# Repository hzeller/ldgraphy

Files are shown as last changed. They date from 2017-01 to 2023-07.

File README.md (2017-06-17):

LDgraphy - Laser Direct Lithography
===================================

http://ldgraphy.org/

A process also known as Laser Direct Imaging.

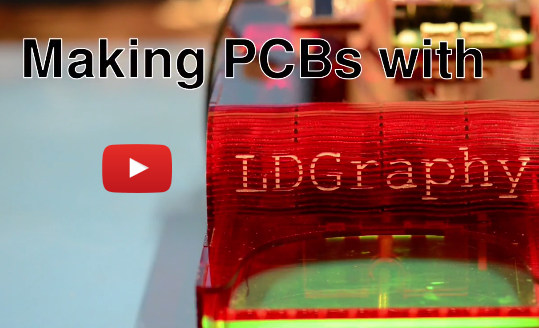
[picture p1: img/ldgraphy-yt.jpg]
First Test
[](https://youtu.be/G9-JK2Nc7w0)

Simple implementation of photo resist exposure using a 405nm laser.
Goal is to have this Open Source/Open Hardware system easy to reproduce with
commonly available parts. The BOM is in the order of $100 including the
Beaglebone Green.

  * 500mW 405nm laser ($30ish)
  * Commonly available polygon mirror scanner (from laser printers) ($20ish)
  * Beaglebone Black/Green to control it all (using the PRU to generate precise
    timings for motors and laser) ($40ish)
  * Stepper motor for linear axis (plus end-stop switches) (scrap box)
  * Photo diode to determine start-of-line (as the polygon mirrors have
    slightly different long faces and also phase-drift over time) (SFH203P)
  * Local electronics: fast Laser diode driver and stepmotor driver (few $$)

Stay tuned for a putting-it-together video once the design is settled.

Here is some [rough design outline][design] in case you are interested in more
details.

Work in Progress
----------------
Currently, the design is [work in progress][LDGraphy-posts] while testing
various different types of commonly available polygon mirrors and lasers. The
[PCBs](./pcb) for the [cape] and the [laser current driver] are in their
first iteration with more focus on easy measurements and removable parts
(e.g. stepper driver and DC/DC converter are external modules) than compact
design. This part of the hardware is likely to change in the
short term; it turns out, for instance, that some polygon mirrors have not
perfectly perpendicular faces. So an additional sensor is needed to correct
for that.

And of course, the software would need a little more bells and whistles
(e.g. a web-server to easily upload Gerber designs).

Having said that, the device is fully operational with a reliable
resolution of ~0.15mm/6mil, which is right up there with basic fab-house
offerings (goal: reliable 0.1mm (4mil) traces and clearance).

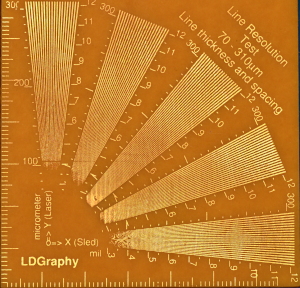
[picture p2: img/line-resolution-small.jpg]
Resolution test
[][resolution]

Compile
-------
This compiles on a BeagleBone Green/Black; it requires the PRU on these
computers for hard realtime-switching of the Laser.

```
git clone --recursive https://github.com/hzeller/ldgraphy.git
```

Install relevant packages. We are reading png-images as input, so we need the
library that helps us with that (probably already installed on your system):
```
sudo apt-get update
sudo apt-get install libpng-dev -y
```

Then compile:
```
cd ldgraphy/src
make
```

To properly prepare the GPIOs and the PRU to be used, you have to install
the device tree overlay on your Beaglebone:
```
cd ldgraphy/device-tree
sudo ./start-devicetree-overlay.sh LDGraphy.dts
```

The input is a PNG image. For converting Gerber files to PNG, see the
`gerber2png` tool in the [scripts/](./scripts) directory.

Usage:
```
Usage:
./ldgraphy [options] <png-image-file>
Options:
        -d <val>   : Override DPI of input image. Default -1
        -i         : Inverse image: black becomes laser on
        -x<val>    : Exposure factor. Default 1.
        -o<val>    : Offset in sled direction in mm
        -R         : Quarter image turn left; can be given multiple times.
        -h         : This help
Mostly for testing or calibration:
        -S         : Skip sled loading; assume board already loaded.
        -E         : Skip eject at end.
        -F         : Run a focus round until Ctrl-C
        -M         : Testing: Inhibit sled move.
        -n         : Dryrun. Do not do any scanning; laser off.
        -j<exp>    : Mirror jitter test with given exposure repeat
        -D<line-width:start,step> : Laser Dot Diameter test chart. Creates a test-strip 10cm x 2cm with 10 samples.
```

Case
----
The current version is made out of [laser-cut acrylic](./hardware)
parts to have it easily and cheaply build for everyone who has
access to a laser cutter (hint: your local Hackerspace might have one).

Here, all electronics is mounted on the top for easier measurements and
such. The final version will fit everything inside.

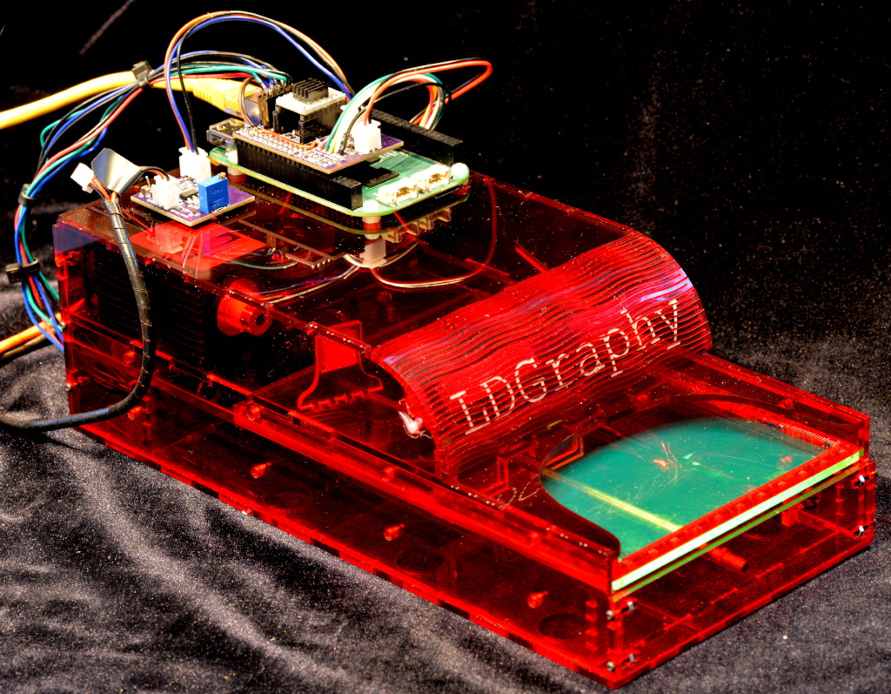
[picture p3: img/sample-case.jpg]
Case
[](./hardware)

Above is current status of the case, which went through some refinements (here
an [earlier case](./img/intermediate-case.jpg) which better shows
the internal arrangement).

This was the first experiment
-------------------------------

#### First Light

| Setup | Result
|---|---
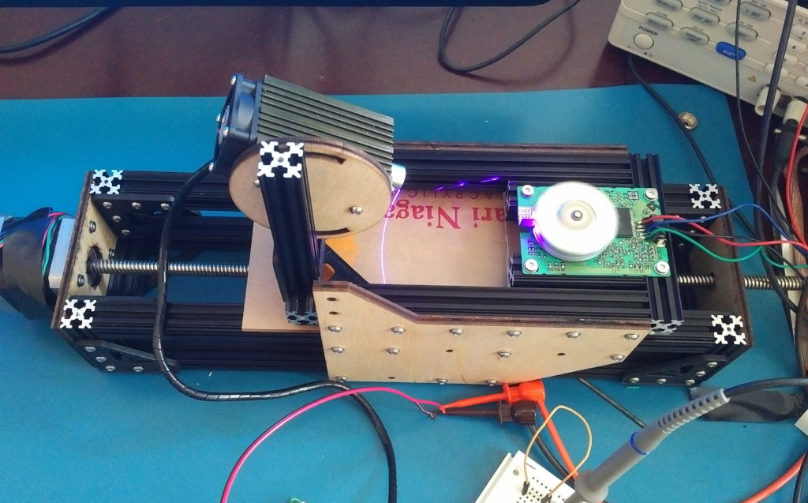
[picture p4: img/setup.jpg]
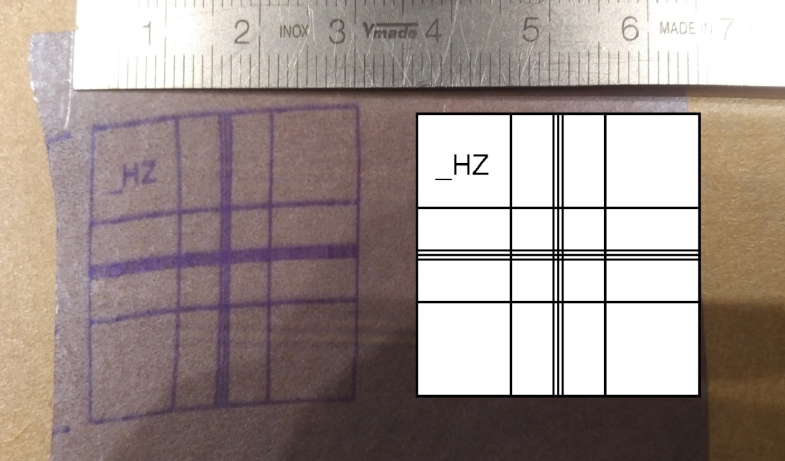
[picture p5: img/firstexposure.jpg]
|  | 

The first test-device was put together with extruded aluminum.
Somewhat crappy first result, but had potential. Exposure time for this 30 mm
long patch was around 90 seconds (for reference: on the right is how the
geometry _should_ look like).

As you can see, the early stages had some issues, e.g. you can't trust the "PLL"
of the mirror to properly lock - it has a phase drift over
time (hence the warped square). The current design has a HSync line sensor.
Overall the [progress] after that improved various
issues seen up to the point where it starts to be usable for PCB work.

[progress]: https://plus.google.com/u/0/+HennerZeller/posts/FeqdPoEZ3AT
[Laser current driver]: ./pcb/laser-drive
[Cape]: ./pcb/cape
[LDGraphy-posts]: https://plus.google.com/u/0/s/%23ldgraphy/top
[run-vid]: ./img/ldgraphy-yt.jpg
[resolution-thumb]: ./img/line-resolution-small.jpg
[resolution]: https://plus.google.com/u/0/+HennerZeller/posts/a8taHWeL5CC
[design]: ./design.md
[case-pic]: ./img/sample-case.jpg

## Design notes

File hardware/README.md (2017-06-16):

Casing
------

The [laser-cut-case.ps](./laser-cut-case.ps) PostScript file is a somewhat
parametrized source for making an acrylic case for LDGraphy.

Use black or dark-red acrylic for all parts except the sled to prevent the
405nm laser to escape in eye-damaging levels. The sled should be cut from
fluorescing material.

**Do not** use glass-clear transparent acrylic for the real machine, a 500mW
laser can blind you!

### How to cut
The file covers several parts, and depending on which you can fit
on your acrylic sheet and/or which you have to re-do, you can choose the ones
to be output in the first section that defines the
[`/print-...`](./laser-cut-case.ps#L28) boolean variables.

The Makefile can create a dxf file that is then usable in any laser cutter, just
call `make`.

There are several colored output layers that have different meaning for your
set-up in the laser cutter:
  * the 'green layer'. Set to scan engraving.
  * the 'blue layer'. Set to vector engraving.

Do the engravings first. Then:
  * the 'black layer'. Cut with outward kerf correction (laser cuts outside).
  * the 'red layer'. Cut with inside kerf correction (laser cuts inside).
  * the 'yellow layer': Set to straight cut, no kerf correction.

Don't cut
  * the 'gray layer' (if `/print-measures` true). Don't cut. Just FYI with measurements and help-lines.

### Customization
If you have a different size PCB that you want to expose, you can customize
the values in the PostScript file an generate a new DXF that should fit your
use-case. Be aware that wider boards means wider exposure angle which in
turn means more variation in focus distance (i.e. on average less sharp image).

Start with modifying `/pcb-w-mm` and `/pcb-h-mm`, watch the PostScript file in
a viewer (e.g. okular). It helps to switch on `/print-measures` while doing
these modifications for more information.
Now, modify the `/scan-angle` so that the polygon mirror fits on the top panel.
You might also need to change `/scan-redirect-mirror-distance` to have the
redirect mirror or its reflected beam not conflict with any object.

### Note
Nearing final state, ready to be used. This is fully parametrized, but
PostScript is not the very best 2D CAD software and updating things is not
so easy. I'd be happy if someone could translate that
into e.g. [Solvespace] CAD. Pull requests welcome :)

### Cut pattern

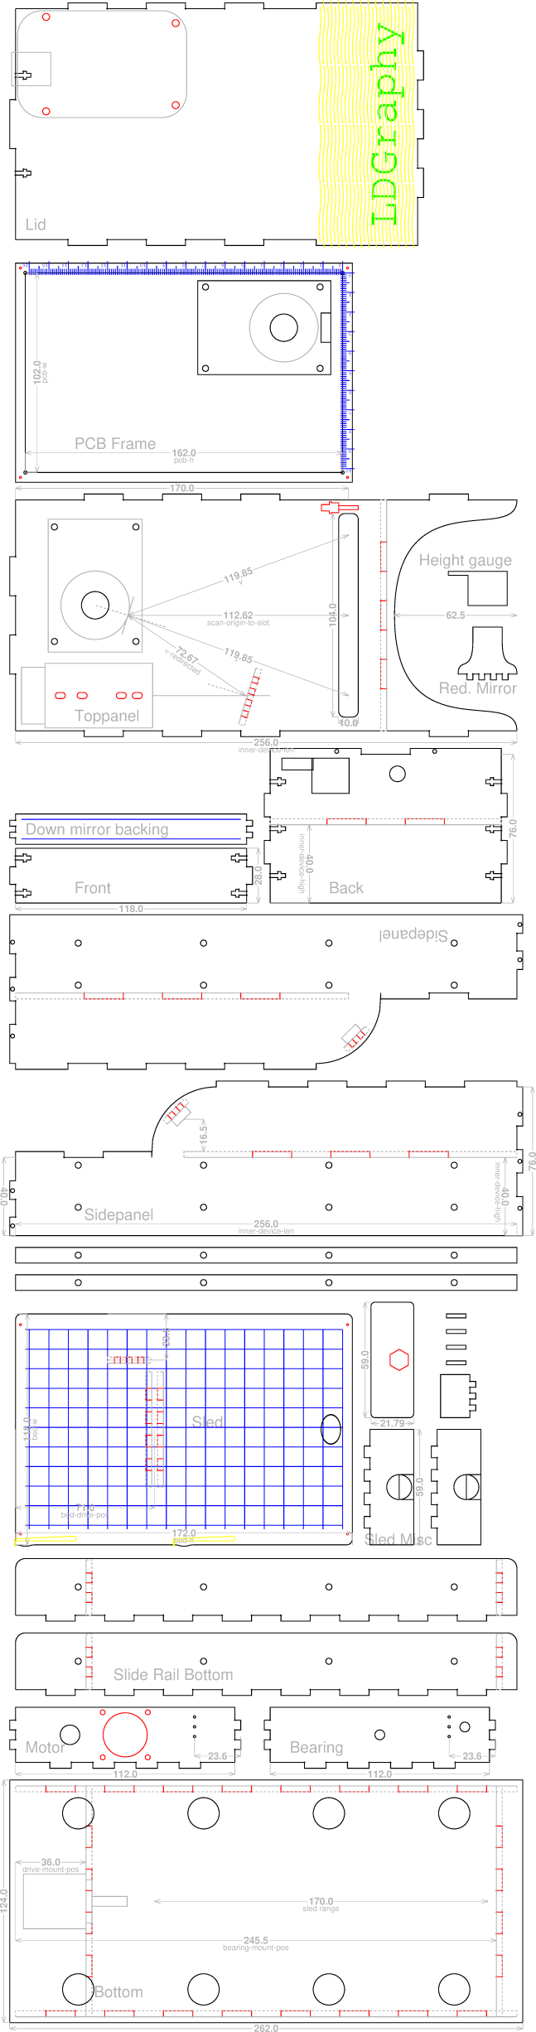
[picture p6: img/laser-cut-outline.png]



[Solvespace]: http://solvespace.com/

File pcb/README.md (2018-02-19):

LDGraphy PCBs
=============

Some boot-strapping required ... we need these PCBs first, before we can make
PCBs :)

  * [Laser driver](./laser-drive): fast current source to drive Lasers. Often,
    the Lasers you can buy come with their own driver, but they are very slow.
    This one is meant to switch >= 1Mhz while behaving as a current source.
  * [Beaglebone cape](./cape): a cape for the
    Beaglebone Black or Green providing all the connections to various
    parts of the set-up. This was the first version mostly for experimenting
    and successfully used.
  * [PocketCape](./pocket-cape): The new cape, ready for the cheaper
    and smaller PocketBeagle.
    Unlike the experimental board that used a DC/DC converter and stepmotor
    driver as separate modules, this has everything on-board.
    It is ready for double-sided boards with two outputs for lasers, polygon
    mirrors and two inputs for horizontal sync detection.

In the current set-up, they are mounted externally to provide easy access for
measuring various aspects. After the dust settles, they will all fit in the
LDGraphy case.

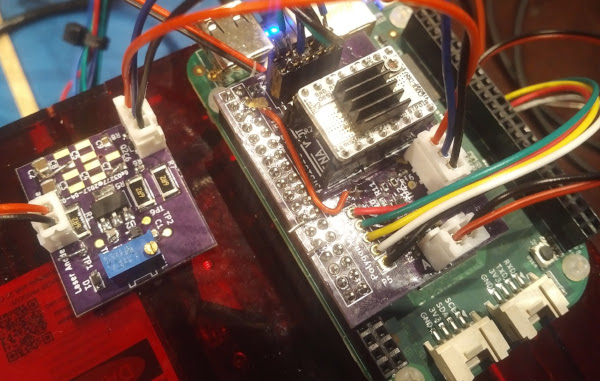
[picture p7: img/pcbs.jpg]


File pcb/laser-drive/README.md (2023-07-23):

Laser Driver Board
===================

Laser driver board, a fast current source switchable with a TTL input. Place
this as close as possible to the Laser with short wires.

Choose `R1`, `R5` and `R7` to achieve desired target current for given laser
(`I ≈ (Vref - 0.6) / (R5+R7)`; Vref=0V..5.6V).

Adjust desired current by reference voltage with trimmer before connecting
laser. Measure current through laser via `(+12V - TP4) / R1`.

Depending on the inductivity of the supply line or desired current, not all
of the 10μ caps (C2..C8) might be needed.

### BOM

Qty | Reference(s)              |  Value    |   Footprint
----|---------------------------|-----------|-----------------------------
2   | C1, C11                   | 100n      | 0603
7   | C2, C3, C4, C5, C6, C7, C8| 10u       | 1210
1   | C9                        | 100n      | 0805
1   | C10                       | 100p      | 0603
1   | D1                        | 5V6 zener | SOD-323
1   | J1                        | CONN_01X03| JST_EH_B3B-EH-A_1x03_P2.50mm
1   | P1                        | LaserOut  | JST_EH_B2B-EH-A_1x02_P2.50mm
1   | Q1                        | BCP5616Q  | SOT-223-3
1   | Q2                        | DMN2058UW | SOT-323_SC-70
3   | R1, R5, R7                | 6R2       | 2512
1   | R2                        | 2k2       | 0603
1   | R3                        | 470       | 0603
1   | R6                        | 680       | 0603
1   | R8                        | 1k        | 0603
1   | RV1                       | 10k       | Multi-turn trimmer (through-hole, 2.54mm pitch)
1   | U2                        |  MIC920   | SOT-353_SC-70-5

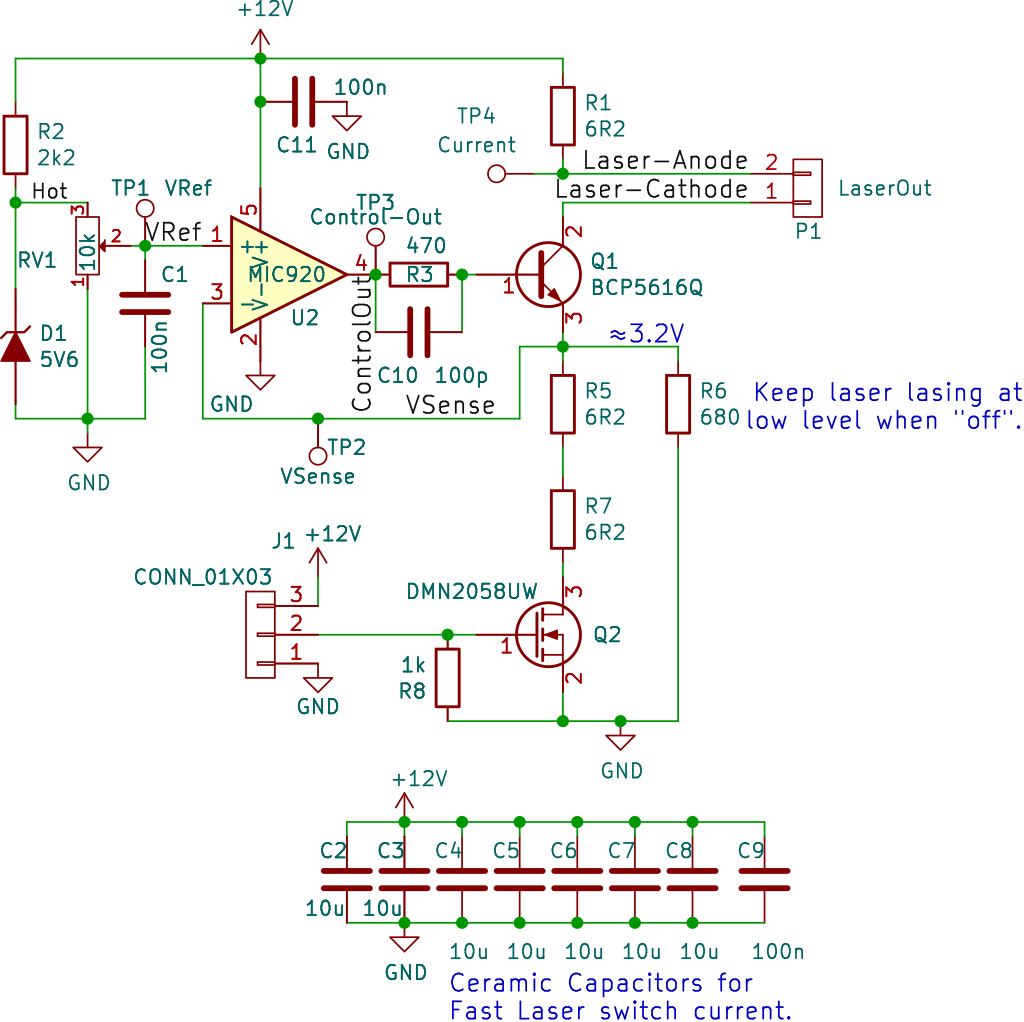
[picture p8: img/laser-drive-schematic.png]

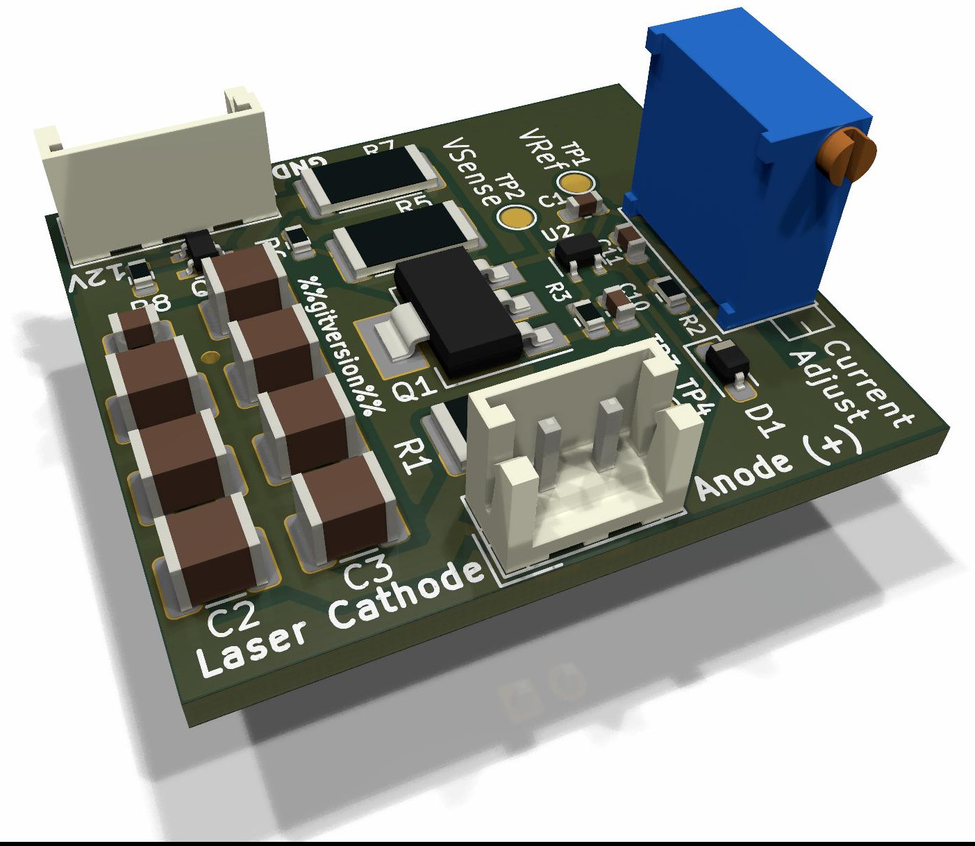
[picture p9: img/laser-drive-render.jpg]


There are probably better ways to have a fast current switching driver for
lasers that don't have a feedback line. Suggestions welcome.

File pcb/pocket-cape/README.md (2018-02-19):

PocketBeagle LDGraphy cape
==========================

A cape for the PocketBeagle, that will allow to expose double-sided boards.

*Work in progress; won't yet work with the current software and case.*

Not only the software is not adapted yet, but this assume as motor
the 28BYJ-48, yet the acrylic case is still using the larger stepper.

So if you want to build something now, I suggest to use
the [experimental cape](../cape).

The board is packed with connectors; all of which are choosen in a way
that it very hard to connect to the wrong one:

| Designator | Type | Description
|---:|:---|:---
| J2 | 2p JST-XH | Supply voltage. 12-16V
| J5, J8 | 3p JST-PH | Laser1, Laser2 output
| J1, J3 | 2p JST-PH | Laser1, Laser2 sync input
| J6, J7 | 5p 0.1" header| Polygon1, Polygon2 mirror
| J4 | 5p JST-XH | Sled stepper 28BYJ-48
| J10 | 8p FFC 0.5mm  | Connector for 320x200 SPI display
| J9 | 4p JST-PH | User-interface buttons
| J11 | USB | USB connector for Wifi dongle

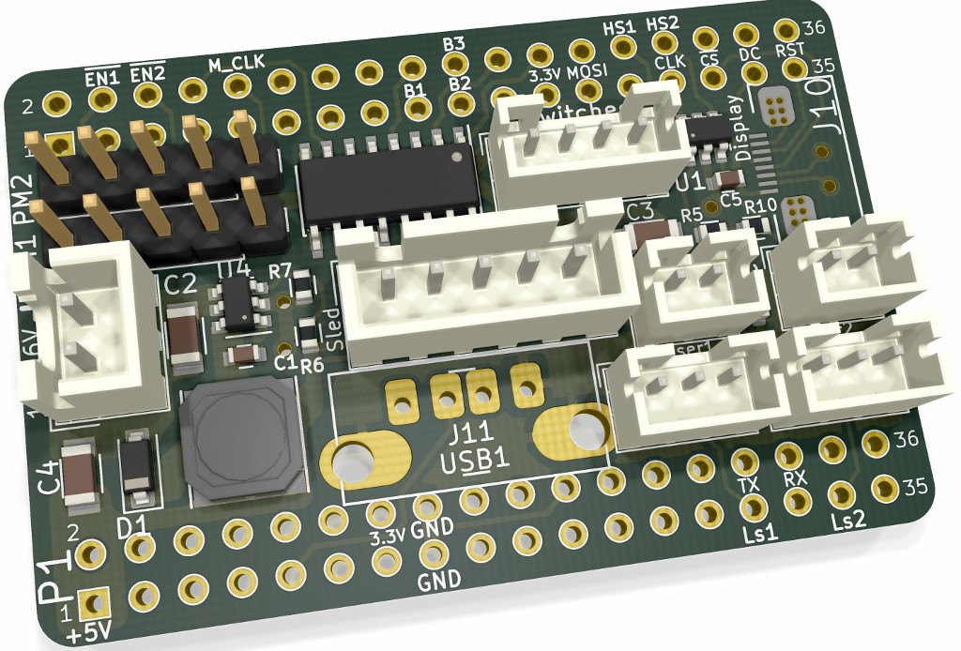
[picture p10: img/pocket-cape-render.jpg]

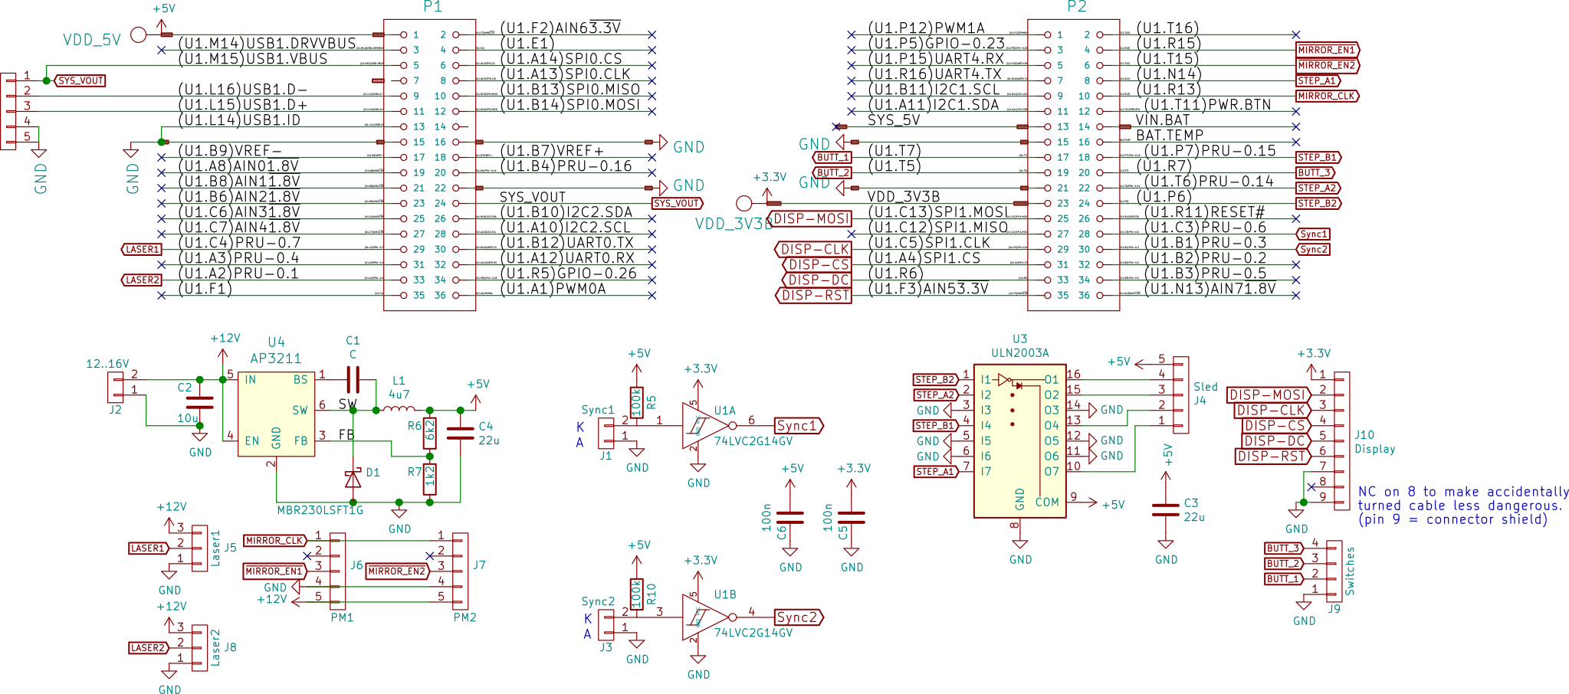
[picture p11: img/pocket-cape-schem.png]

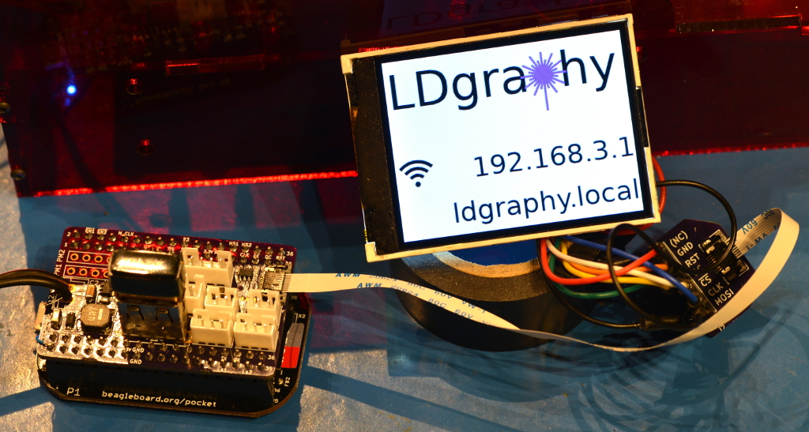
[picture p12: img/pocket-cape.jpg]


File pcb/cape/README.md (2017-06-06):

LDGraphy Beaglebone Black cape
==============================

This is for the experimental set-up. This is not meant to
be final, it focuses on easy measurement and mostly being a break-out for
connectors for other parts. The final board will have all the parts that are now
external modules integrated on one board.

  * Single 12V supply (uses a MP1584 based module to generate 5V supply for
    Beaglebone).
  * Inputs
     - Connector for photo diode used for the horizontal sync detection.
       Amplifier and Schmitt Trigger with fast OpAmps ([MIC920] datasheet)
       and steep enough slew-rate to generate acceptable output for digital
       inputs (also, same as used in the [laser driver](../laser-drive) to keep
       BOM small).
     - Two end-switches inputs.
     - One "user interface"-button input.
  * Outputs
     - Laser output connector for external [laser driver](../laser-drive).
     - Polygon mirror pulses and enable via 5-pin Polygon mirror connector.
     - Stepper motor (In this set-up: simply using a Pololu module)

(TODO: update schematic: there is now a cap accross R14)

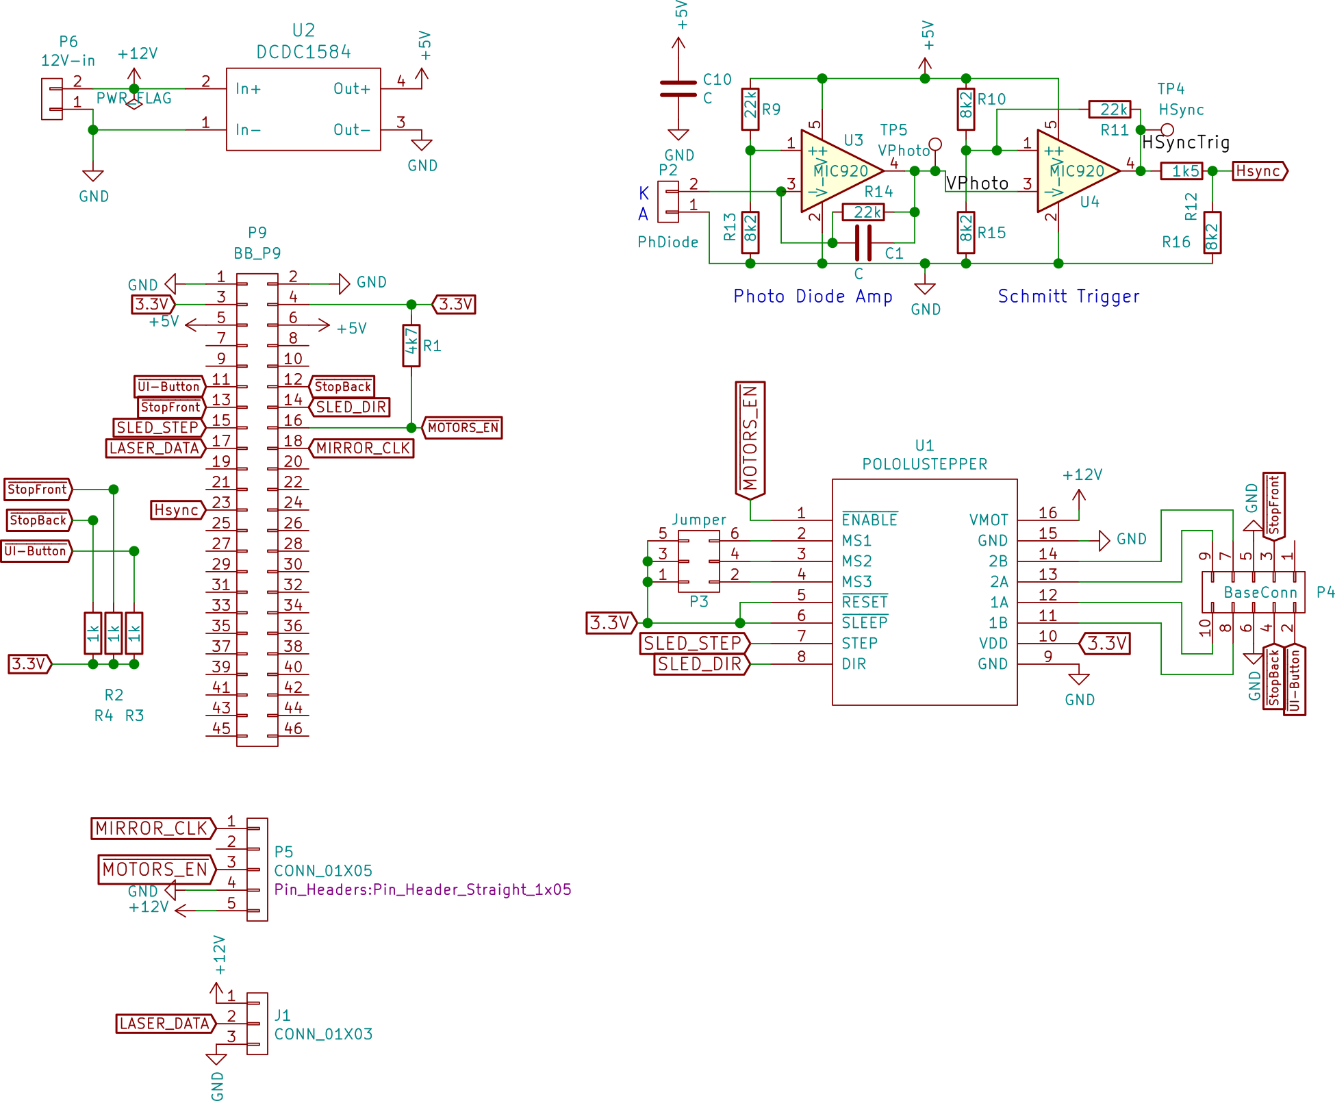
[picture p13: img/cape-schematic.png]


[MIC920]: http://ww1.microchip.com/downloads/en/DeviceDoc/mic920.pdf

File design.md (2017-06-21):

LDGraphy design overview
========================

### Theory

At its core, LDGraphy is a switched laser, a rotating mirror that
moves the dot in a scan-line and a sled that moves the photoresist-coated PCB
forward.

Laser scanning is very simple and cheap to do with common components these
days. Lasers with a wavelength of 405nm (which is close to the peak-sensitivy
of dry-film photoresist) can be found cheaply with around 500mW power.

As for scanning, there are several techniques. A common one is to have a mirror
that rotates to deflect a laser. Since it would take a while for a mirror
to turn around full 360° after a segment is scanned, they come as
a polygon mirror: a polygon that has mirror-reflective edges.
A typical mirror that is used in Laser printers 6 sides; you notice that
the actual mirror face is not that high - but we only need to deflect a laser dot.

| Top | Side
|---|---
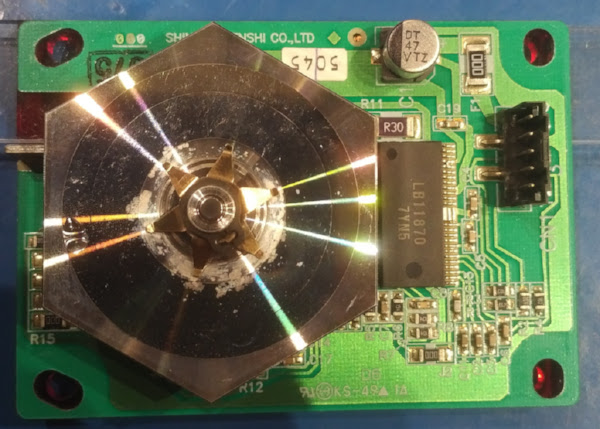
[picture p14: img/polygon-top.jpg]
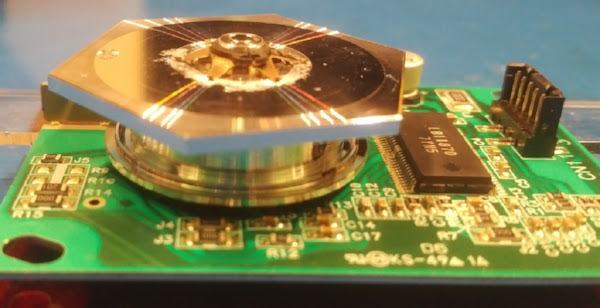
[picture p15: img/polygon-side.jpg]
|   | 

With this hexagon, we can project a 120° arc (each mirror
face is 60°, so the angle between incident ray and reflected ray is 120°).

Here, we just shine (a fast blinking) laser at an angle from the top, it is
reflected at the rotating mirror and projected downwards.
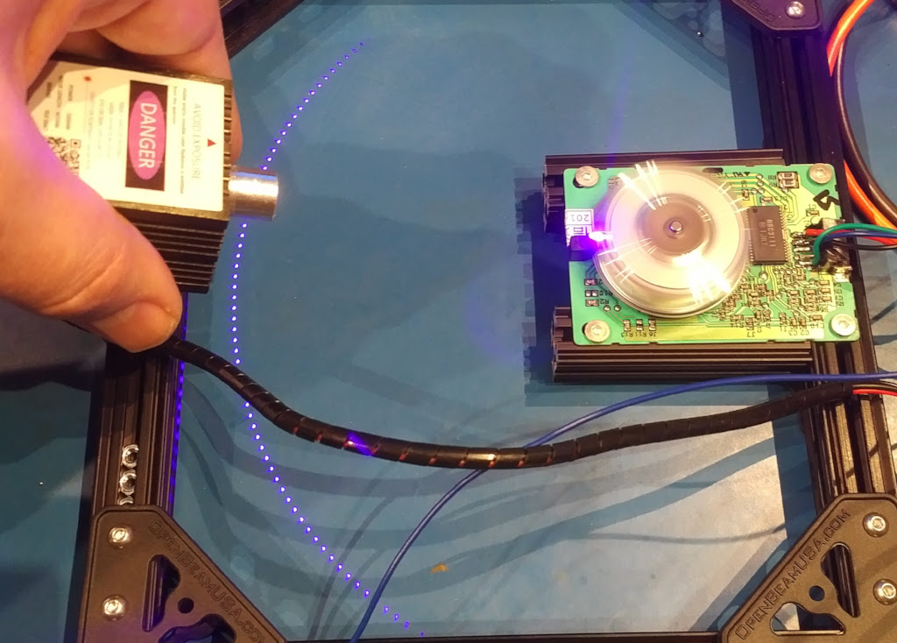
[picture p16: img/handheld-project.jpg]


#### Direct angled arc exposure
We can make a scanning device with this simple set-up if we correct for the
arc distortion in software; in fact, in an early experiment for LDGraphy
I was doing exactly that:

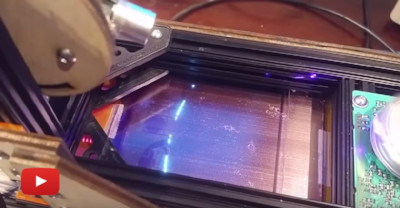
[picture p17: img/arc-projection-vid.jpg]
Early experiment
[][arc-project-vid]

There are advantages for this set-up: we can utilize a large fraction of the
laser on-time by covering the majority of the available scan range.
The scanning laser is "almost" in focus for the scan range where it hits
the board.

This is a simulation of such a scanning in which we use 105° out of 120°
(the laser is off only for 15 degrees). We can see that the laser dot is oval
in the extreme angles but also even in the center. This is because the actual
focal plane of the laser (indicated with a gray disc at the sharpest focus)
is hitting the surface at an angle, resulting in an oval exposure.

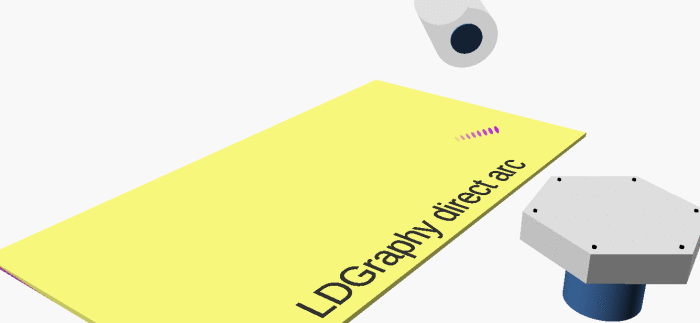
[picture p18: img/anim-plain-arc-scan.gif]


This set-up is very simple to build, but the oval exposure dot is an issue.
Also it is very sensitive to angle variations: just small changes in the
shallow angle moves the projected arc-line forward and backwards.

#### Cone mirror arc exposure
This could be fixed, if we had a mirror that points the laser-arc downwards, so
that it hits the resist perpendicularly and is also always in focus.
The mirror would need to be a circular segment with a downwards
angle -- essentially a segment of
an inner slice of a cone. Now we hit the photo resist always at a sharp
focus point, even for the wide scan angle of 105 degrees as the geometry
keeps the focal plane of the laser exactly on the exposed surface.

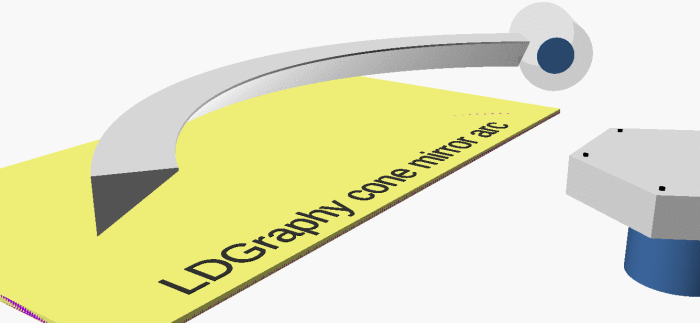
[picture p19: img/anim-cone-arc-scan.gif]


However, making custom mirrors in such a shape at home is not easy.

Possible ways:
 * With a lathe: this would essentially be a 45° bevel on the inside of a
   large diameter stainless steel pipe with a wall thickness of about 2-3mm.
   Then mirror finish polishing this bevel. Stainless steel or aluminum are
   both nicely polisheable, so these could be materials of choice.
 * [John M. suggests on his blog][NaN-cone-mirror] to build such a mirror using
   laser cut parts that, snapped together, defining the shape.

We want to build this machine with minimal accessible tools, so these techniques
have to be explored if they can be done with minimal tools. Till then, let's
see what else we can do.

#### Straight mirror line exposure
We can simplify and use a straight mirror to project downwards to get a line.
However, the focus point then is of course not always in the plane of the
photo sensitive material. In particular if we cover a large scan angle, the
focus variants are significant.

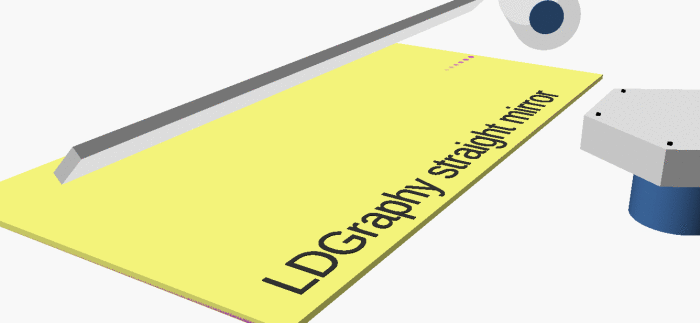
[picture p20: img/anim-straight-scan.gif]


The exposure point now is very large at the fringes. We could alleviate some of
it by "plunging" the focus plane below the surface at the center, but it will
still be too much of a variant.

The advantages for the home-build is, that this works with a very simple straight
mirror (easy to come by with) and does not have the problem of being sensitive
to the shallow angle variations like the angled direct arc exposure.

The issue though is the focus, even more pronounced than in the direct arc scan.

#### F-Theta lens corrected line exposure
In professional scanning applications, a so-called [f-theta lens][f-theta-images]
is used to keep a straightly projected laser dot always focused to a plane.

If you take apart a laser printer, you will see a lens set in the
laser assembly: that is the f-theta lens.

However, this is also somewhat out of reach for the hobbyist to make (though
I still consider to try making one with transparent acrylic). It also does not
seem to be available as off-the-shelf part like the Polygon mirrors and the laser
does (you can get them, but they are very expensive).

If you find some, it is probably meant for a laser printer and optimized for
infrared light not UV light.

What else can we do ?

#### Straight mirror line exposure with small throw

If we choose to do the straight projection, but only use the 'center piece'
and limit ourselves to a smaller angle, the focus variation is not _that_ much
and we get an acceptable compromise in exposure dot size.

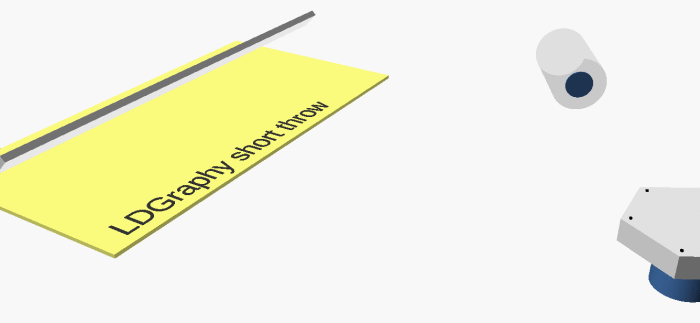
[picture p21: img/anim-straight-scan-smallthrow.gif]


We don't need any special mirror or lens. The disadvantage is, that we only
can use part of the time of the laser: if we use 40° scanning out
of 120°, we only use the laser for 1/3 of the time (you see the laser is
dark for a long period in the illustration). Also, we need much more space as
we need to be further away to cover the same PCB width.

### Design Options Review
Let's review our options

   * Angled direct arc exposure
     mirror:
       * :thumbsup: fewest parts needed; almost full use of the laser; No light losses.
       * :thumbsdown: focus plane intersects with exposed board at an angle creating oval dots; susceptible to small angle changes; large build.

   * Cone mirror arc exposure
       * :thumbsup: almost full use of laser; no light losses; hitting resist
       	  perpendicularly; always in focus; very compact.
       * :thumbsdown: Requires to build a custom shaped mirror.

   * Straight mirror line exposure with _large_ throw
       * :thumbsup: easy to build; very compact.
       * :thumbsdown: very noticeable focus issues in far angels.

   * F-Theta lens corrected line exposure
       * :thumbsup: Almost full use of the laser; hitting resist perpendicularly; always in focus.
       * :thumbsdown: Requires to build a custom shaped lens; might have optical
         losses in the material.

   * Straight mirror line exposure with _small_ throw
       * :thumbsup: easy to build; focus issues less pronounced than with
          large throw.
       * :thumbsdown: need longer exposure time; large build.

Overall, the most promising is the cone mirror solution: it creates sharp focus
points, makes good use of the laser time and building a custom mirror
is somewhat more feasible than building a f-theta lens.

However, since ease-of-build for everyone with limited access to tools is a
priority, we start with the small throw line exposure for this first version
of LDGraphy - it doesn't require any manufacturing of a mirror and is a
good compromise.

### Practice

#### Scanning

This is how the current LDGraphy device looks like. From the top, we can
see all relevant components for the laser scanning:

| Drawing | Reality
|---|---
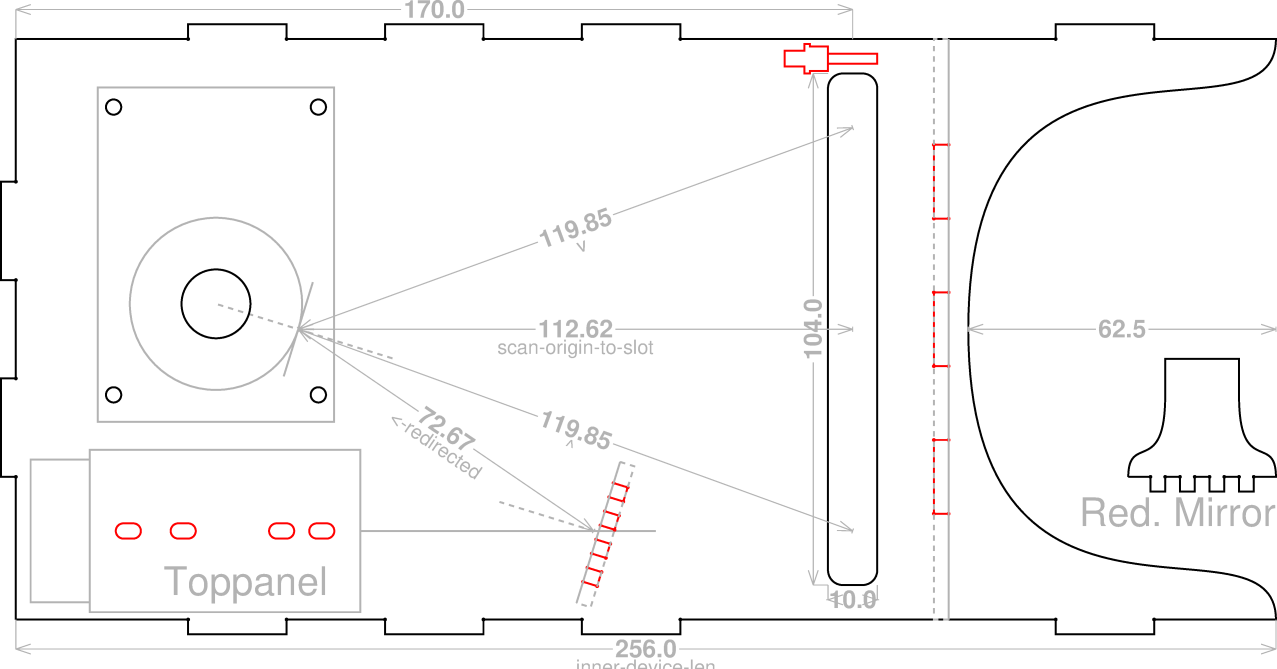
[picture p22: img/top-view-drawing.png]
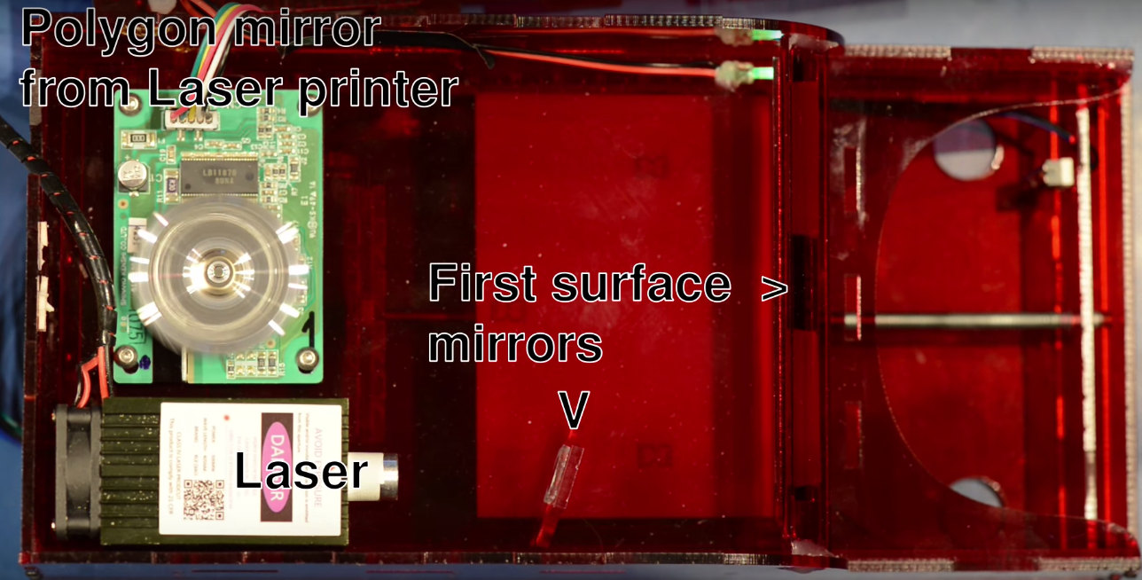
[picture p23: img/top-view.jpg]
|[See full drawing here][hardware] | 

To keep things more compact, the laser is mounted in one corner and the light
is redirected onto the polygon mirror. But other than that, this is exactly
as discussed above. There is a long mirror on the side that is pointing
downwards, a little hard to see from above, so lets look from the back, with
some rough indication of the laser path:

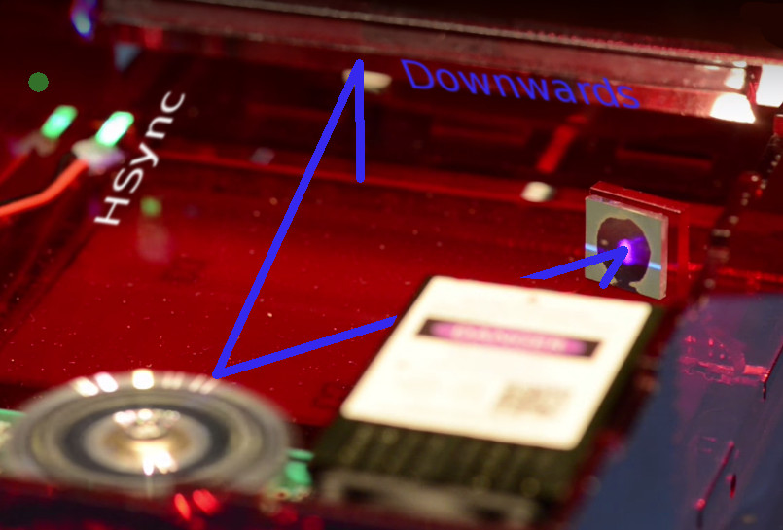
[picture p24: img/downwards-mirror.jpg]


When the polygon mirror is rotating, the laser point passes through a slit onto
the surface to be exposed.

On the left, you see a fluorescing piece of material that has a photo diode
attached. This is our horizontal sync (HSync) to detect when a laser line starts.

##### Issues

There is an issue that I discovered with some cheap polygon mirrors: the six
mirror faces have a little variation and not being entirely parallel to the
rotating axis, so project lines up and down a little, depending on the face.
So what needs to be done is to have another sensor to count mirror faces, and
then correct for this after a calibration step in software.

#### Moving the sled

The sled is moved with a stepper motor and a threaded rod. This rod does not
need to be CNC quality ball-screw, a simple screw from the hardware store is
sufficient. Why ? We only need to move in one direction, so we don't care about
backlash issues.

Here is how the base looks like, housing the motor and the threaded rod. The rod
is 'mounted' to the shaft of the motor with a heatshrink tubing (and a little
expoxy butting these together). A nut is not directly mounted to the sled but
to a slab of acrylic. You also see both the limit-switches:

| Just drive | .. with sled
|---|---
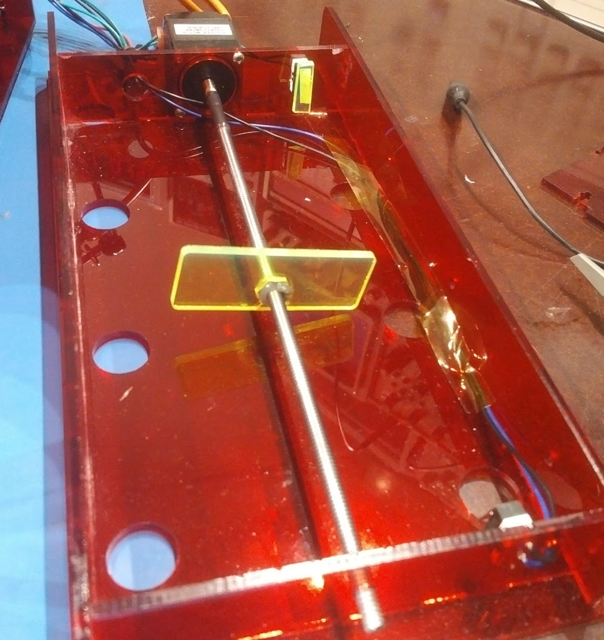
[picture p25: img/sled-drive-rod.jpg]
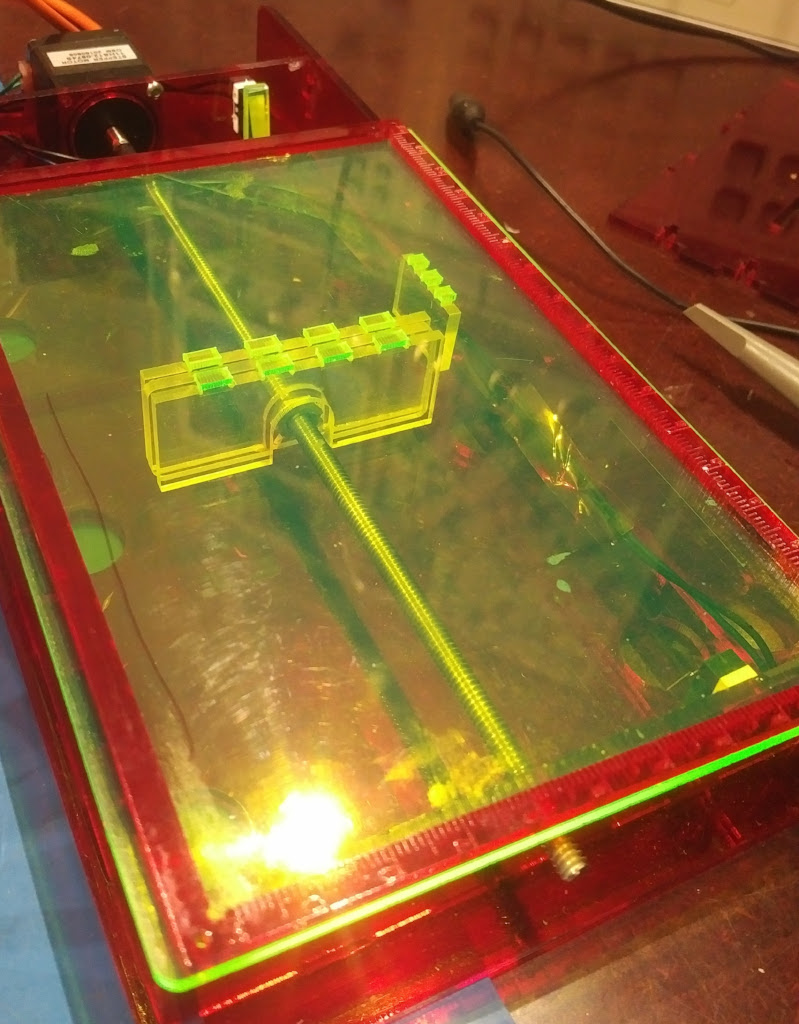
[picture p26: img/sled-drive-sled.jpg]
| | 

This allows us to have a separate sled that then sits on top of the moving
slab of acrylic. The design detail here is, that it allows to drive the sled
forward and backward, but has freedom to move in other directions: this can
be used to essentially be immune to 'wobble' from the cheap threaded rod.
In the current test version of LDGraphy, I have a horribly wobbling rod that
I found in a corner of my workshop.

You [see the wobble in the video :movie_camera:][ldgraphy-vid]; It still produces
acceptable quality

[Resolution test][resolution]

#### Electronics

Everything is controlled by a BeagleBone Black or Green. It has the nice property
that it is a common ARM machine running Linux (so offers the comfortable
environment of a full operating system including networking and can do all the
work like converting Gerbers and do image processing), but it also has
a built-in Programmable Realtime Unit (PRU) - a fast (200Mhz), independent
microcontroller essentially to help do the timing-accurate parts interfacing
the hardware.

We need this to accurately
generate the pulses to control the polygon mirror, switch on the Laser at the
right times (we have about 2Mhz pixel clock), and generally keep track of where
the laser is. And before you ask: of course, this could be done with an external
Cortex M4 or so, connected via SPI to some other computer (it would be more
expensive of course, but it works). I just had the BeagleBone lying around and
had used the PRU in a [previous project][beagleg].

The laser requires a current source, in our case it needs to be switched in the
low Mhz range. Some lasers (that you get from e.g. Aliexepress) already have a
"TTL driver", but they are utterly low frequency (50ish kHz), so this is why this
project needed its own [laser current driver] (not perfect yet, but works).

Right now, all the electronics is attached to the outside of the case, for easy
hacking and scope-probe access. Eventually, all these parts will
go inside the case.



[resolution-thumb]: ./img/line-resolution-small.jpg
[resolution]: https://plus.google.com/u/0/+HennerZeller/posts/a8taHWeL5CC
[beagleg]: https://github.com/hzeller/beagleg
[Laser current driver]: ./pcb/laser-drive
[early-experiment]: ./img/arc-projection-vid.jpg
[arc-project-vid]: https://youtu.be/8tyT4CI-1io
[ldgraphy-vid]: https://youtu.be/G9-JK2Nc7w0
[hardware]: ./hardware#cut-pattern
[f-theta-images]: https://www.google.com/images?q=f+theta+lens
[NaN-cone-mirror]: http://notanumber.net/archives/228/circular-mirror-idea-laser-lithography

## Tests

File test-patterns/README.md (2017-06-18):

Test Patterns
=============
Various test-patterns used to calibrate and test the machine.
Postscript files, use Makefile to generate hi-res PNG that can be fed to
LDGraphy.

#### Low res examples

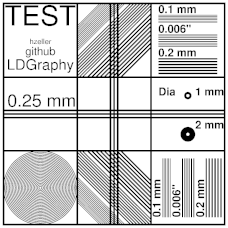
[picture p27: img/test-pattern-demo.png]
test-pattern

[test-pattern](./test-pattern.ps)

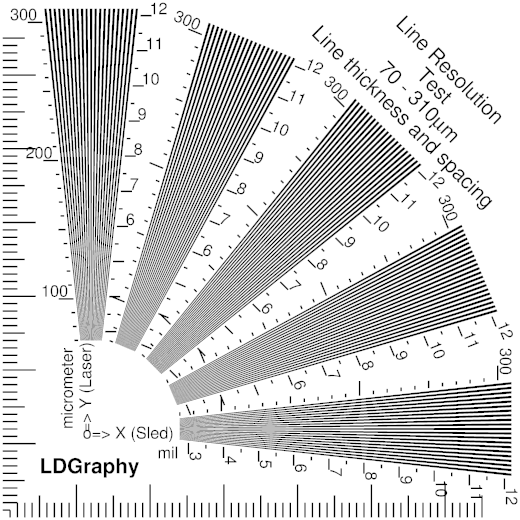
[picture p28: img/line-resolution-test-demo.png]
line-resolution-test

[line-resolution-test](./line-resolution-test.ps)

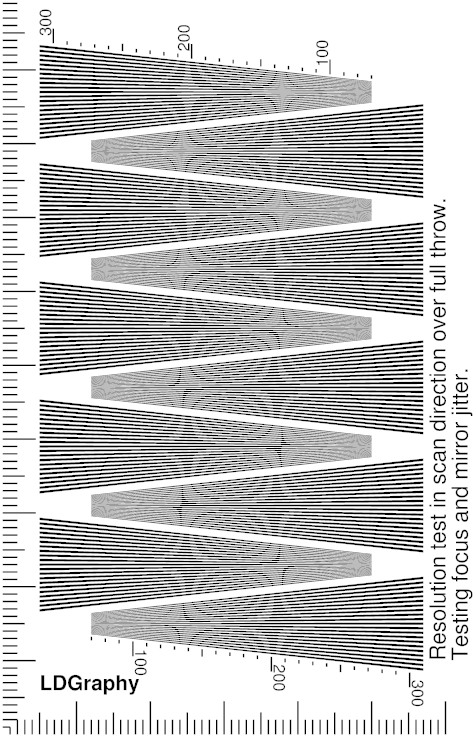
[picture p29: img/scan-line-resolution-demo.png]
scan-line-resolution-demo

[scan-line-resolution-demo](./scan-line-resolution.ps)

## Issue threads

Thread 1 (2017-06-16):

Raspberry Pi instead of beaglebone

jvegaf, 2017-06-16:
First of all congrats for the project, it's awesome !!!

Why you use beaglebone ?

It's possible use a raspberry pi ?

Thanks !

hzeller, 2017-06-16:
Only if you use and program an external fast microcontroller to sent the laser pulses at the right time. Right now, LDGraphy relies on the Programmable Realtime Unit of the BeagleBone to do that.
The BeagleBone Green is $39, the Raspberry Pi $35, so that is $4 well worth spent for reduced complexity.

Closed 2017-06-16.

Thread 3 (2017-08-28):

Not an issue, but a (stupid) question

Pepetruen0, 2017-08-28:
Hi, I'm seeing that the laser driver has a note stating "there is now a cap accross R3." As I'm a newbie and English is not my primary language, can I have a brief explanation of what this means? Also, what size capacitor do I need to use for this?

Thanks.

hzeller, 2017-08-29:
This means that there needs to be an additional capacitor in parallel to `R3`, which has not been reflected yet in the schematic or printed circuit board.
I have fudged the capacitor in with what I had lying around, I think it was around 100pF.

Pepetruen0, 2017-09-04:
Wait, when you say "fudged" do you mean "I got away with" or "totally destroyed"? Just to be sure.

hzeller, 2017-09-05:
'fudged' means that I choose the value without much calculation after having measured the outcome on an oscilloscope. I hacked it into the existing board by just soldering the capacitor on top of the R3. It works well.

Not sure what you want to do with your circuit above, but the 100pF needs to be across `R3` not `R2`.

Pepetruen0, 2017-09-05:
Whoops, my bad. I meant something like this, would it work?

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

hzeller, 2017-09-05:
Yeah, this looks good. The value is somehwere in the order of 22pF to 100pF. They will essentially suppress unstable behavior like this:

https://plus.google.com/u/0/+HennerZeller/posts/g9reVCg4bnE

Pepetruen0, 2017-09-06:
Awesome, thank you so much for your patience!

Closed 2017-09-06.

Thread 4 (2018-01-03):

Positive or Negative Photoresist

marcwolf1960, 2018-01-03:
Hi.
Are you using positive or negative photoresist.  And are you exposing where you want the coper to stay.. or exposing where you want to remove it.
I have seen some experiments re using paint and burning the paint off using a laser but that tends to leave a lot of copper on the boards.

Many thanks

hzeller, 2018-01-03:
I am using the photo resist gel that is exposed where the copper should stay. However the other works as well (but as far as I heard a little less light sensitive). You can choose the mode of exposure with the `-i` option to the ldgraphy binary.

The laser is not powerful enough to burn away paint, so you can't use it for that, but the photo-resist method is possibly a lot more accurate.

christianlupus, 2018-01-03:
@hzeller you are using negative resist then.
As far as I have learned, positive resist is inherently more accurate because for the negative resist a local polymerization is triggered by the light. This process might spread out and blur an edge. However this was in a lecture about microprocessing of silicon. So the average size of a pcb is much larger than the problems involved there....

> The laser is not powerful enough to burn away paint, so you can't use it for that, but the photo-resist method is possibly a lot more accurate.

You mean any photo-method to be more accurate, right? I am not sure I get the meaning of your statement.

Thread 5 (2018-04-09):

start-devicetree-overlay.sh

phpscriptru, 2018-04-09:
debian@beaglebone:~/ldgraphy/device-tree$ sudo ./start-devicetree-overlay.sh LDGraphy.dts
make: 'LDGraphy-00A0.dtbo' is up to date.

Adding LDGraphy overlay
./start-devicetree-overlay.sh: line 69: /sys/devices/bone_capemgr.*/slots: No such file or directory
cat: '/sys/devices/bone_capemgr.*/slots': No such file or directory
debian@beaglebone:~/ldgraphy/device-tree$

VasUtkin, 2018-04-09:
another problem:

make: 'LDGraphy-00A0.dtbo' is up to date.
Adding LDGraphy overlay
./start-devicetree-overlay.sh: line 69: echo: write error: Invalid argument
 0: PF----  -1
 1: PF----  -1
 2: PF----  -1
 3: PF----  -1
debian@beaglebone:~/ldgraphy/device-tree$

hzeller, 2018-04-09:
are you running a 3.18 kernel?

phpscriptru, 2018-04-09:
Latest version: 4.9.82-ti-r102
(Debian 9.3 2018-03-05 4GB SD IoT)

hzeller, 2018-04-09:
yeah, they changed the way overlays work on newer kernels. Either you adapt that or switch to a distribution with an older kernel.

atmelletje, 2023-05-12:
> yeah, they changed the way overlays work on newer kernels. Either you adapt that or switch to a distribution with an older kernel.

I looked at this for a long time and now is the time (as I now have more free time) to start with it. I'm a mechanical engineer but do not have much clue about software repo's distros.  could you tell me what version distri will work as there are many of them.
my BBB is a rev C with 4+ debian flashed.  thank you in advance

Roel

hstarmans, 2023-05-12:
Hey @atmelletje,

I worked on ldgraphy for some time and then moved to Amaranth HDL.
You should check out the library here (https://github.com/hstarmans/ldgraphy/tree/master)

Something you could look into are;
   1) how do i blink blink the laser using a PRU
        https://github.com/hstarmans/ldgraphy/tree/master/scripts/pru_tests/blinklaser_channel1
```python
#!/usr/bin/python3
""" blinklaser1.py - test script for the Firestarter
blinks the laser 3 times with a period of 6 seconds
"""python
from uio.ti.icss import Icss

pruss = Icss('/dev/uio/pruss/module')
pruss.initialize()
core = pruss.core0
core.load('blinklaser1.bin')
core.run()
print('Waiting for core to halt')
while not core.halted:
    pass
```
After the laser test I would run;
  - test polygon https://github.com/hstarmans/ldgraphy/tree/master/scripts/pru_tests/spinpolygon
  - test diode https://github.com/hstarmans/ldgraphy/tree/master/scripts/pru_tests/photodiodetest
  - try to stabilize https://github.com/hstarmans/ldgraphy/tree/master/scripts/pru_tests/stabilizer

Note that in my install notes,
  i tell you exactly which image I used
https://rcn-ee.net/rootfs/bb.org/testing/2019-09-08/stretch-iot/bone-debian-9.10-iot-armhf-2019-09-08-4gb.img.xz

This could be a good way to start, good luck!

atmelletje, 2023-05-12:
Thanks Hstarmans. dit helpt me op de juiste weg te komen.

Roel

hstarmans, 2023-05-12:
Your welcome!  Henner zeller wilde uiteindelijk ook naar een FPGA gaan en heeft hier nog een tijdje aan gewerkt. Dit werk staat in de beagleg repository in de FPGA branch.
Ik heb er behoorlijk wat tijd ingestorken en mijn oplossing staat nu hier https://github.com/hstarmans/hexastorm/blob/master/src/hexastorm/lasers.py
De python code wordt geconverteerd naar HDL en dit gaat dan de FPGA in via icestorm.
De variant waar ik momenteel aan werk heeft de FPGA op de printplaat en de motor is verwerkt in het PCB.

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

De lenzen zijn optioneel maar geven wel een significante prestatie verbetering.

atmelletje, 2023-05-13:
Hey Rik,

ik ben geen code writer, moet et meer van een werkende installatie hebben. ik ga het op een andere manier gebruiken dmv een drum met film te beichten.  (filmbelichter/photplotter) mijn intentie is om het voor meerdere toepassingen te kunnen gebruiken zoals Pad Printing. waarbij de "hexagon/square" de drum zal zijn. Dat is de bedoeling hiervan.

Anyways! installation fails because of a missing file ( libpng-dev)

g++ -std=c++0x -Wall -W -Wno-unused-function -I../am335x_pru_package/pru_sw/app_loader/include -D_XOPEN_SOURCE=500 -mtune=cortex-a8 -march=armv7-a -O3 -c  image-processing.cc -o image-processing.o
image-processing.cc:21:17: fatal error: png.h: No such file or directory
 #include <png.h>
                 ^
compilation terminated.
Makefile:50: recipe for target 'image-processing.o' failed
make: *** [image-processing.o] Error 1

Roel

hstarmans, 2023-05-13:
@atmelletje, did you install the relevant packages as outlined by Henner Zeller?

**From the documentation;**
Install relevant packages. We are reading png-images as input, so we need the library that helps us with that (probably already installed on your system)
```
sudo apt-get update
sudo apt-get install libpng-dev -y
```
There are also other solutions as turning part of the code into comments, changing the compilation order etc. This might bring you closer to identifying the issue.

Mechanical skills can be very useful for this project but you will also need extensive electronic and software skills.  If you have a different setup, you will for sure need to adapt the code.
There is company in Eindhoven which used to illuminate a rotating drum with a laser (4Pico), although i can no longer find that system on their site.

I can imagine that with a high motivation and a willingness to learn to code, you can end up with some sort of setup in a couple of months / weeks.
Still, it will be hard to scale or monetize and most likely is doomed.

atmelletje, 2023-05-13:
the problem is that the Libpng-dev can't be found with an update. during the update, several source packages return an error.
I know enough about electronics and mechanics to get this to work.

Croot@beaglebone:/var/lib/cloud9#sudo apt-get install libpng-dev -y
Reading package lists... Done
Building dependency tree
Reading state information... Done
E: Unable to locate package libpng-dev
root@beaglebone:/var/lib/cloud9#

hstarmans, 2023-05-13:
There are roughly two options;
   1) find a compiled binary, look online for your distro and platform and add a source.
       in ubuntu this is known as adding a ppa.
   2) create a binary yourself by compiling libpng from its source code, this possible takes longer and is a
       bit more complicated.

I am sure you have the skills and determination to do it, but given the fact you did not build one makes you underestimate the time required.
The devil is also in the last 20 percent. Once you reach proof of concept stage you will realize you still need to do 80 percent of the work.

atmelletje, 2023-05-14:
> i tell you exactly which image I used
https://rcn-ee.net/rootfs/bb.org/testing/2019-09-08/stretch-iot/bone-debian-9.10-iot-armhf-2019-09-08-4gb.img.xz

this image has vanished :)

hstarmans, 2023-05-14:
@atmelletje, I would go to a recent image. My code mainly relies on the work of mvduin (another dutchmen :-))
https://github.com/mvduin/py-uio
He actually takes care of the interaction between scrips that are run on top of the beagle bone PRU.
His work is also maintained. You should then be able to test the hardware.
You can also sent me an email and I can pick it up from there; hstarmans@hexastorm.com.
I am in Mexico at the moment, so there can be some delay.

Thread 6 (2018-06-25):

Alternative focus improvement

connyg, 2018-06-25:
Hi Henner,

I have been following your LDGraphy project for about a year, have you done more work on that?
Last thing you were experimenting with was the cone mirror to improve the focus and achieve a higher resolution.

In a discussion about galvo & fiber laser arrangements a guy recently had an interesting idea:
Instead of using a f-theta lens he thought about lasering zones and move the z-axis for the focus.

That could be an idea for LDGraphy, too.
It could have two modes, one for "regular resolution" (6 mil) that would do a PCB in one pass on one z-level.
And a second mode, "high resolution" that would expose the PCB in multiple stripes for different z-focus zones and have some mechanic to move the focus by a few mm.
Softwarewise you would only "black out" certain areas of a line, on basis of the zone calculation.
There could be a zone for each mm of focus.

If I am calculating correctly if you have 250mm distance diode-focus point and an angle of 25 degrees for the laser, the focus deviation is some 6mm.
Possibly 2mm for one zone is already providing enough improvement, then there would be 3 zones = 3 passes. For 1mm there would be 5 or 6 passes.

There could be different solutions to move the focus:
- move the laser unit (rail and lead screw)
- move the small mirror in front of the laser unit (rail/lead screw)
- rotate the lens with belt/gear

For the lens it needs fixing of the wobbly gear (maybe external mount on rail?), moving the small mirror changes the z arrangement of laser, mirror, facet mirror, moving the laser unit seems quite doable.

What do you think?

Kind regards,
Conny

hstarmans, 2018-06-26:
Hey Conny,

I have looked into another solution with a transparent where an f-theta lens is not needed, see [hexastorm](https://hackaday.io/project/21933-open-hardware-transparent-polygon-scanner). Resolutions down to 20 micrometers can be reached. In general, it is possible to do what you suggest. The process will take longer and will likely require an extra actuator.
The key question is; will there be a business case!? This is much harder.

Best,
Rik

connyg, 2018-06-26:
Hi Rik,

looked at the hexastorm pages and it's quite an interesting idea to simply use optical refraction through two parallel edges.

There's two key questions left for me:

1) Can I manufacture the transparent polygon with maker tools? What material is it from, how did you make it?

2) Am I understanding correctly that for exposing a 100mm wide PCB I need a transparent polygon that has an edge length (if it's a quadron) of about that size? In your demo device there is a quadron of about 3-4cm edge length and you state the scan length is 24mm maximum. Then I'd need a quadron that's larger than 100mm?
Of course I could scan a PCB in 4 lanes, but then it (or the laser unit) needs to move in X direction to allow for the lanes and the setup is more complex plus the exposure process takes 4x again.

As these quadrons are not available to buy or not trivial to manufacture "at home" it seems that's not a "maker" solutions in the end.

Regarding business case: I am looking at this from a maker / hobbyist point of view, I am not interested in a business case. But in a cool & working solution that I can manufacture on my own, without buying expensive components like F-Theta lenses...
Of course such device could be sold, even in masses, if it had a price tag of a "few hundred" dollars, let's say 200-300.

hstarmans, 2018-06-26:
1. No, you can't manufacture them with maker tools. I had them custom made in China,
    square prisms i.e. 4 sides   a = 30mm x 30 mm, thickness = 2mm, Faces 60/40 < 5 arc min,   Chamfers 0.10 – 0.30mm, Edges Polished 60/40. The material was quartz and the price is 55 dollar a piece, with a Minimum Order Quantity (MOQ) of 10 so 550 dollars.

  2. You understand this correctly. There are two options; a large prism or multiple scans. The large prism is physically not feasible as you can't spin a polygon off this size on commercially available polygon motors.

It's good to hear you are doing this for fun and not the money. In the end, and I have seen many projects, I would advice you to look for a project where you can also break even and make a little money. Or a project which has some other benefits, being good for your career or for the environment / man kind. It will be hard to sustain them otherwise.
There is a need for laser scanner in microfluidics, bioprinting and photo-polymerization. The first customers will most likely be Industry and R&D institutes. Although it is admirable to make something for the masses. Making money from a 200-300 dollar product is really hard. The prusa i3 costs something like [919 euro](https://shop.prusa3d.com/en/3d-printers/53-original-prusa-i3-mk2s-3d-printer.html#). Most vendors in this market, like [ultimaker](www.ultimaker.com), moved to small business and have a starting price around 2000-3000 euro.

connyg, 2018-06-26:
Ok, so "unfortunately" both assumptions were correct :-)
Well, I have a nice "day job" that gives me enough, no need to earn money with my hobby/spare time stuff - 3D printing (including modding the printers), electronics and laser cutting/engraving (including modding the laser cutter).
I am doing those things just for personal challenge, to see what can be done and to try / learn new things.
Of course it is hard to make money of a mass market product in that segment and I don't feel like engaging in that segment. :-)

hstarmans, 2019-05-27:
Working version of the transparent scanner is shown here; https://youtu.be/SofTXG5s_MA .

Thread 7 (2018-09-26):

Python port

hstarmans, 2018-09-26:
Hey Henner,

I started porting your code to Python. Progress is available here [python port](https://github.com/hstarmans/ldgraphy/tree/master/scripts/pru_tests). In specific, the stabilizer folder. I have been able to get my polygon stable with your code for the firestarter board. I did not need a Schmitt trigger. The signal looks quite crisp without it.
I hope the Python port will make your assembly driver code more accessible for other developers. In addition, I am not very experienced with C++ so wanted to ditch it anyway :-).

Best,

Rik

hzeller, 2018-09-27:
Have fun!
(I'll stick with C++, it is much easier to read and deal with than Python)

Closed 2018-09-27.

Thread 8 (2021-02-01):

About the project

mralperem, 2021-02-01:
Hello sir,

Do you still work on this project?

hzeller, 2021-02-01:
I am using the device I built, but not much changes since then. It should be usable as-is, but might need some updates as the Kernel interfaces to the PRU changed.

I have built a version of [cone arc mirror](https://github.com/hzeller/ldgraphy/blob/master/design.md#cone-mirror-arc-exposure) design, but then other projects got my attention, so I never fitted that entirely.
There is also a new [cape for the pocket beagle](https://github.com/hzeller/ldgraphy/tree/master/pcb/pocket-cape), I only tested parts of it, as it uses a bit of a different stepper motor control.

Though good point, I should revisit this project and update it to latest things and get the pocket beagle going.

hstarmans, 2021-02-02:
I made two forks of the project; [ldgraphy](https://github.com/hstarmans/ldgraphy) and [hexastorm](https://github.com/hstarmans/hexastorm).  The cone arc mirror is an interesting idea. [Nextscantechnology](https://nextscantechnology.com/) uses large mirrors in laser scanning and Formlabs uses a parabolic mirror. I always thought the cone arc mirror idea would be hard to manufacture but this is also determined by which accuracy you require.
At the moment, I am trying to write a FPGA core for Beagle G.  I do not intend to rewrite the rest of the beagle G code base. I actually already have a repo for it [FPGAG](https://github.com/hstarmans/FPGAG) but is not close to working at the moment.

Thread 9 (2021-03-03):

Raspberry Pi support

arslan437, 2021-03-03:
Is there any way to use Raspberry Pi ?

hzeller, 2021-03-03:
Not right now, as it relies on the PRU of the Beaglebone Black.

There is a plan to integrate an FPGA at some point (and I think @hstarmans has something brewing), which would allow to use a simple Raspberry Pi and output to SPI.

I have that on my TODO list, but don't hold your breath as I also have a ton of other projects going on :)

arslan437, 2021-03-03:
Thanks for the fast reply.

Can you share any document or link that explains how can we draw a dot? what pwm duty cycle or frequency ? or any other info that is help full

hzeller, 2021-03-03:
Drawing a dot is essentially switching on the laser at the exact time the mirror moved it to the right place; if you want to know the details, you have to read the [code that does the synchronization](https://github.com/hzeller/ldgraphy/blob/master/src/laser-scribe-pru.p).
The highlevel [design document](https://github.com/hzeller/ldgraphy/blob/master/design.md) explains some more context.

The laser is either on or off, so in order to get more exposure, you have to stay at one point and wait for multiple cycles sending multiple dots there. This is the 'exposure factor` in the ldgraphy binary (option `-x`): it slows down the forward movement of the board.

If you just want to use the device and draw a dot, it is as simple as creating a PNG file with a dot and giving it to `ldgraphy` - it does the rest.

hstarmans, 2021-03-04:
@arslan437 , here is an instruction video of my current setup https://youtu.be/Ri6DAneEzw4
The board can be found here https://github.com/hstarmans/firestarter/tree/master/pi_hat  This all works and has been tested on Raspberry pi. The current code is in migen. I am upgrading it to nmigen and adding motion.

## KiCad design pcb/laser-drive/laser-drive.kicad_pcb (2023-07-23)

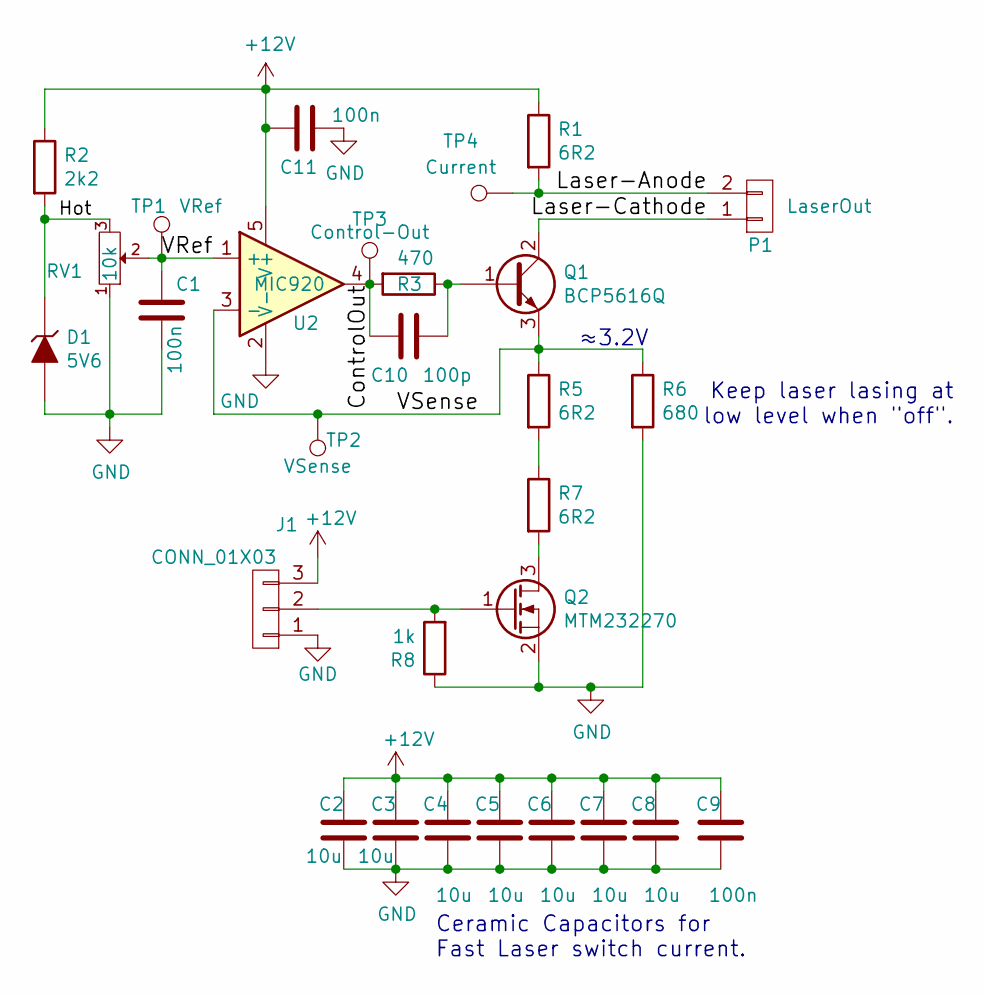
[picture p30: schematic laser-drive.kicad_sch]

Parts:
C1, C11: 100n; C_0603_1608Metric
C2, C3, C4, C5, C6, C7, C8: 10u; C_1210_3225Metric
C9: 100n; C_0805_2012Metric
C10: 100p; C_0603_1608Metric
D1: 5V6; D_SOD-323_HandSoldering
J1: CONN_01X03; JST_EH_B3B-EH-A_1x03_P2.50mm_Vertical
P1: LaserOut; JST_EH_B2B-EH-A_1x02_P2.50mm_Vertical
Q1: BCP5616Q; SOT-223-3_TabPin2
Q2: MTM232270; SOT-323_SC-70
R1, R5, R7: 6R2; R_2512_6332Metric
R2: 2k2; R_0603_1608Metric
R3: 470; R_0603_1608Metric
R6: 680; R_0603_1608Metric
R8: 1k; R_0603_1608Metric
RV1: 10k; Potentiometer_Bourns_3296X_Horizontal
TP1: VRef; TestPoint_Pad_D1.5mm
TP2: VSense; TestPoint_Pad_D1.5mm
TP3: Control-Out; TestPoint_Pad_D1.5mm
TP4: Current; TestPoint_Pad_D1.5mm
U2: MIC920; SOT-353_SC-70-5

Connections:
+12V: C2.1, C3.1, C4.1, C5.1, C6.1, C7.1, C8.1, C9.1, C11.2, J1.3, R1.1, R2.1, U2.5 (V+)
/ControlOut: C10.2, R3.2, TP3.1, U2.4
/Hot: D1.1 (K), R2.2, RV1.3
/Laser-Anode: P1.2, R1.2, TP4.1
/Laser-Cathode: P1.1, Q1.2 (C)
/VRef: C1.1, RV1.2, TP1.1, U2.1 (+)
/VSense: Q1.3 (E), R5.1, R6.1, TP2.1, U2.3 (-)
GND: C1.2, C2.2, C3.2, C4.2, C5.2, C6.2, C7.2, C8.2, C9.2, C11.1, D1.2 (A), J1.1, Q2.2 (S), R6.2, R8.1, RV1.1, U2.2 (V-)
unnamed: J1.2, Q2.1 (G), R8.2
unnamed: C10.1, Q1.1 (B), R3.1
unnamed: Q2.3 (D), R7.2
unnamed: R5.2, R7.1

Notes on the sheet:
≈3.2V
Keep laser lasing at low level when "off".
Ceramic Capacitors for Fast Laser switch current.

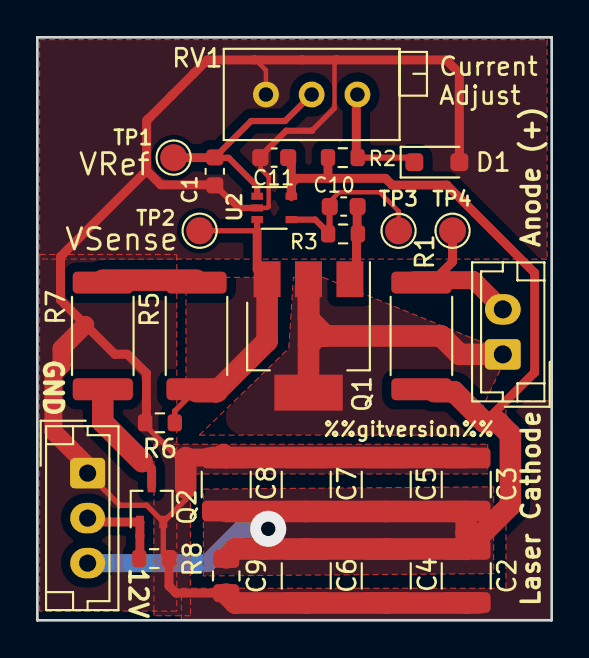
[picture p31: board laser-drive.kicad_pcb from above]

Board: 2 copper layers, 28.6 x 32.4 mm, 29 parts (0 on the bottom side), 12 nets.

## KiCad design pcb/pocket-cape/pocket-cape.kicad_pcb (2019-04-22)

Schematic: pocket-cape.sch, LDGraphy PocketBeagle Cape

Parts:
C1: C; C_0603_1608Metric
C2: 10u; C_1206_3216Metric
C3, C4: 22u; C_1206_3216Metric
C5, C6: 100n; C_0603_1608Metric
D1: MBR230LSFT1G; D_SOD-123
J1: Sync1; JST_PH_B2B-PH-K_1x02_P2.00mm_Vertical
J2: 12..16V; JST_XH_B2B-XH-A_1x02_P2.50mm_Vertical
J3: Sync2; JST_PH_B2B-PH-K_1x02_P2.00mm_Vertical
J4: Sled; JST_XH_B5B-XH-A_1x05_P2.50mm_Vertical
J5: Laser1; JST_PH_B3B-PH-K_1x03_P2.00mm_Vertical
J6: PM1; PinHeader_1x05_P2.54mm_Vertical
J7: PM2; PinHeader_1x05_P2.54mm_Vertical
J8: Laser2; JST_PH_B3B-PH-K_1x03_P2.00mm_Vertical
J9: Switches; JST_PH_B4B-PH-K_1x04_P2.00mm_Vertical
J10: Display; FlatFlexConn-08; PartNo SFv8R-4STBE1HLF
J11: USB1; USB-A-Vertical
L1: 4u7; L_Taiyo-Yuden_NR-60xx
P1, P2: TH-2X18-(35MIL-DIA)-W_O-SILK
R5, R10: 100k; R_0603_1608Metric
R6: 6k2; R_0603_1608Metric
R7: 1k2; R_0603_1608Metric
U1: 74LVC2G14GV; SOT-23-6
U3: ULN2003A; SOIC-16_3.9x9.9mm_P1.27mm
U4: AP3211; SOT-23-6

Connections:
+12V: C2.1, J2.2, J5.3, J6.5, J7.5, J8.3, U4.4 (EN), U4.5 (IN)
/(U1.A1)PWM0A: P1.36
/(U1.A3)PRU-0.4: P1.31
/(U1.A8)AIN0~1.8V: P1.19
/(U1.A10)I2C2.SCL: P1.28
/(U1.A11)I2C1.SDA: P2.11
/(U1.A12)UART0.RX: P1.32
/(U1.A13)SPI0.CLK: P1.8
/(U1.A14)SPI0.CS: P1.6
/(U1.B2)PRU-0.2: P2.32
/(U1.B3)PRU-0.5: P2.34
/(U1.B4)PRU-0.16: P1.20
/(U1.B6)AIN2~1.8V: P1.23
/(U1.B7)VREF+: P1.18
/(U1.B8)AIN1~1.8V: P1.21
/(U1.B9)VREF-: P1.17
/(U1.B10)I2C2.SDA: P1.26
/(U1.B11)I2C1.SCL: P2.9
/(U1.B12)UART0.TX: P1.30
/(U1.B13)SPI0.MISO: P1.10
/(U1.B14)SPI0.MOSI: P1.12
/(U1.C6)AIN3~1.8V: P1.25
/(U1.C7)AIN4~1.8V: P1.27
/(U1.C12)SPI1.MISO: P2.27
/(U1.E1): P1.4
/(U1.F1): P1.35
/(U1.F2)AIN6~3.3V: P1.2
/(U1.L15)USB1.D+: J11.3, P1.11
/(U1.L16)USB1.D-: J11.2, P1.9
/(U1.M14)USB1.DRVVBUS: P1.3
/(U1.N13)AIN7~1.8V: P2.36
/(U1.P5)GPIO-0.23: P2.3
/(U1.P12)PWM1A: P2.1
/(U1.P15)UART4.RX: P2.5
/(U1.R5)GPIO-0.26: P1.34
/(U1.R11)RESET#: P2.26
/(U1.R16)UART4.TX: P2.7
/(U1.T11)PWR.BTN: P2.12
/(U1.T16): P2.2
/BAT.TEMP: P2.16
/FB: R6.2, R7.1, U4.3 (FB)
/SW: C1.2, D1.1 (K), L1.1, U4.6 (SW)
BUTT_1: J9.2, P2.17
BUTT_2: J9.3, P2.19
BUTT_3: J9.4, P2.20
DISP-CLK: J10.3, P2.29
DISP-CS: J10.4, P2.31
DISP-DC: J10.5, P2.33
DISP-MOSI: J10.2, P2.25
DISP-RST: J10.6, P2.35
GND: C2.2, C3.2, C4.2, C5.1, C6.1, D1.2 (A), J1.1, J2.1, J3.1, J5.1, J6.4, J7.4, J8.1, J9.1, J10.7, J10.9, J11.4, J11.5, P1.13, P1.15, P1.16, P1.22, P2.15, P2.21, R7.2, U1.2 (GND), U3.3 (I3), U3.5 (I5), U3.6 (I6), U3.8 (GND), U3.11 (O6), U3.12 (O5), U3.14 (O3), U4.2 (GND)
LASER1: J5.2, P1.29
LASER2: J8.2, P1.33
MIRROR_CLK: J6.1, J7.1, P2.10
unnamed: C1.1, U4.1 (BS)
unnamed: J1.2, R5.1, U1.1
unnamed: J3.2, R10.1, U1.3
unnamed: J4.1, U3.10 (O7)
unnamed: J4.2, U3.13 (O4)
unnamed: J4.3, U3.15 (O2)
unnamed: J4.4, U3.16 (O1)
STEP_A1: P2.8, U3.7 (I7)
STEP_A2: P2.22, U3.2 (I2)
STEP_B1: P2.18, U3.4 (I4)
STEP_B2: P2.24, U3.1 (I1)
SYS_5V: P2.13
SYS_VOUT: J11.1, P1.5, P1.24
Sync1: P2.28, U1.6
Sync2: P2.30, U1.4
VDD_3V3B: C5.2, J10.1, P2.23, U1.5 (VCC)
VDD_5V: C3.1, C4.1, C6.2, J4.5, L1.2, P1.1, R5.2, R6.1, R10.2, U3.9 (COM)
VIN.BAT: P2.14
~MIRROR_EN1: J6.3, P2.4
~MIRROR_EN2: J7.3, P2.6

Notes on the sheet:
NC on 8 to make accidentally turned cable less dangerous. (pin 9 = connector shield)

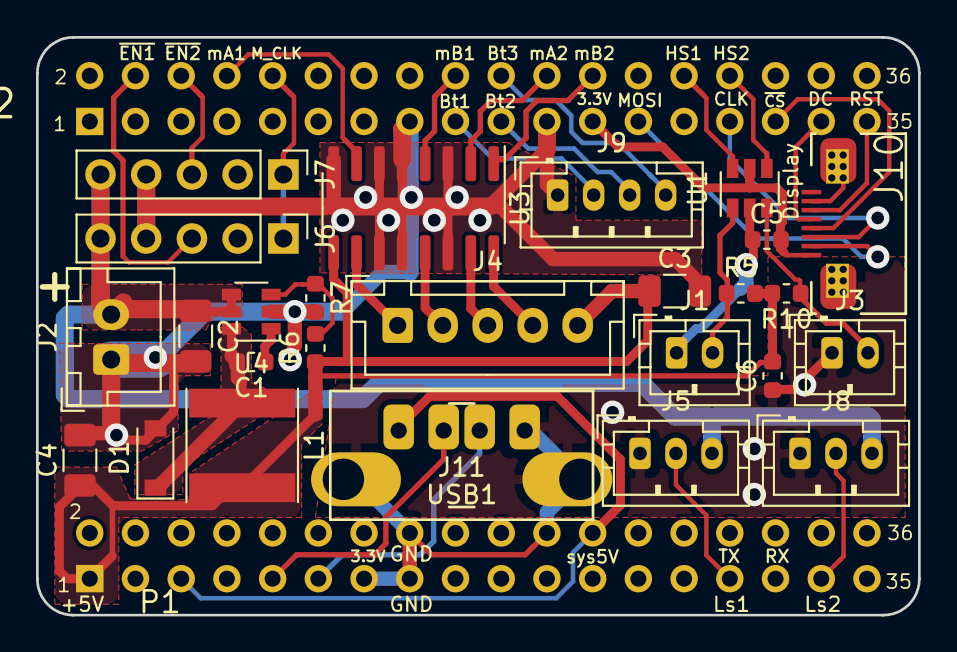
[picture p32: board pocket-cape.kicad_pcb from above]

Board: 2 copper layers, 49.0 x 32.1 mm, 28 parts (0 on the bottom side), 35 nets.

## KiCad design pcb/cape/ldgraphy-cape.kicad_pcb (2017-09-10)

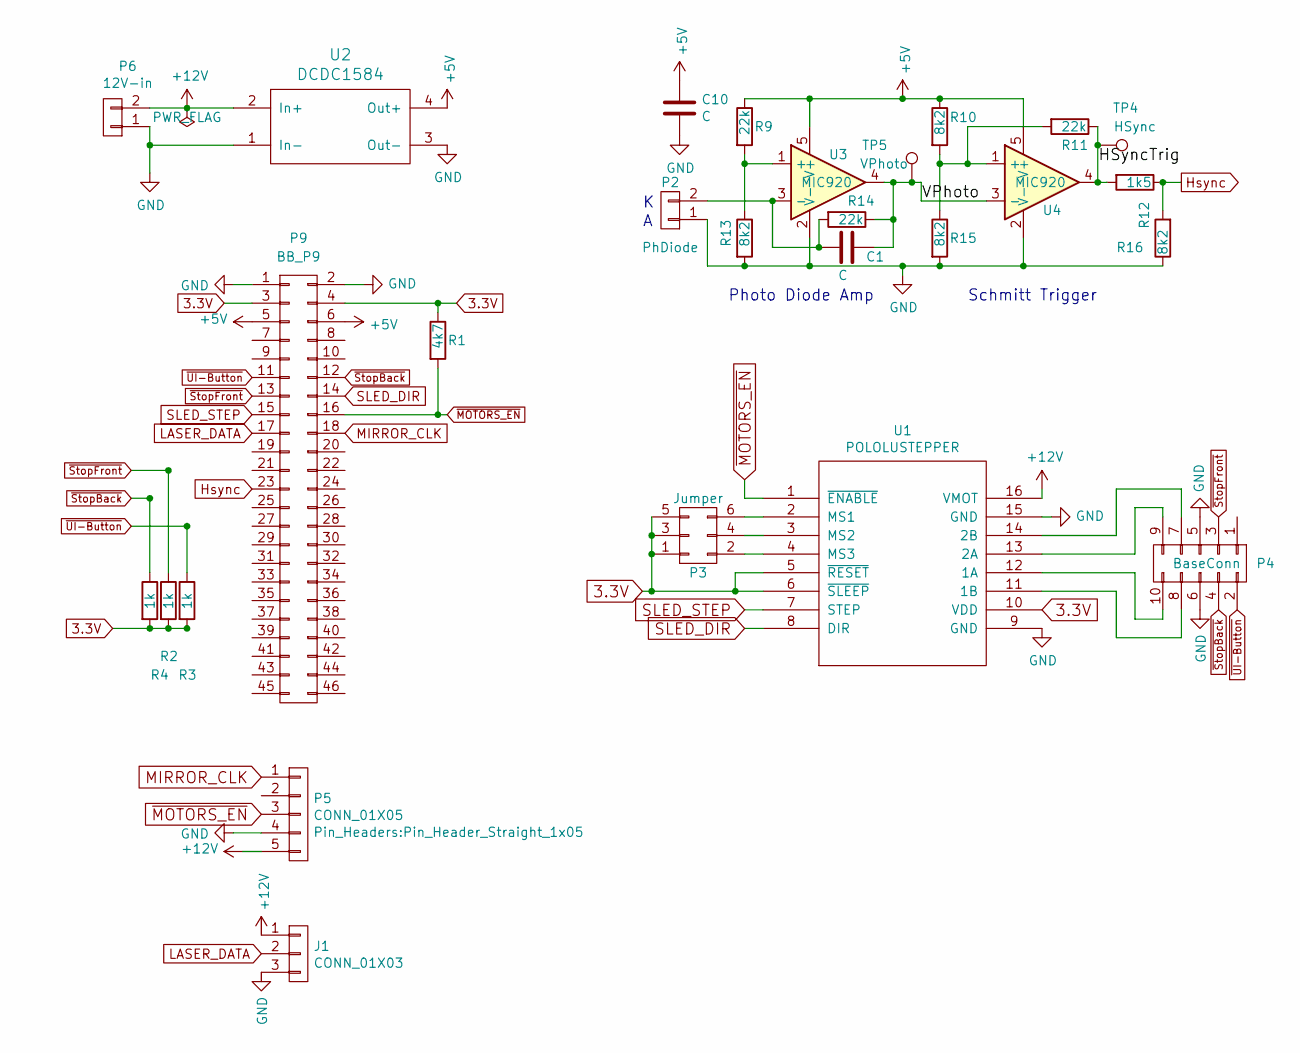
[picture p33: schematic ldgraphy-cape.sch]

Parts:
C1, C10: C; C_0603
J1: CONN_01X03; Pin_Header_Straight_1x03_Pitch2.54mm
P2: PhDiode; Pin_Header_Straight_2x01_Pitch2.54mm
P3: Jumper; Pin_Header_Straight_2x03_Pitch2.54mm_SMD
P4: BaseConn; Pin_Header_Straight_2x05_Pitch2.54mm_SMD
P5: CONN_01X05; Pin_Header_Straight_1x05
P6: 12V-in; Pin_Header_Straight_1x02_Pitch2.54mm
P9: BB_P9; Pin_Header_Straight_2x18_Pitch2.54mm
R1: 4k7; R_0603
R2, R3, R4: 1k; R_0603
R9, R11, R14: 22k; R_0603
R10, R13, R15, R16: 8k2; R_0603
R12: 1k5; R_0603
TP4: HSync; Measurement_Point_Round-SMD-Pad_Small
TP5: VPhoto; Measurement_Point_Round-SMD-Pad_Small
U1: POLOLUSTEPPER; POLOLU
U2: DCDC1584; dcdc-mp1584
U3, U4: MIC920; SOT-353_SC-70-5

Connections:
3.3V: P3.1, P3.3, P3.5, P9.3, P9.4, R1.1, R2.2, R3.2, R4.2, U1.5 (~RESET), U1.6 (~SLEEP), U1.10 (VDD)
+5V: C10.1, P9.5, P9.6, R9.1, R10.1, U2.4 (Out+), U3.5 (V+), U4.5 (V+)
+12V: J1.1, P5.5, P6.2, U1.16 (VMOT), U2.2 (In+)
/HSyncTrig: R11.1, R12.2, TP4.1, U4.4
/VPhoto: C1.1, R14.1, TP5.1, U3.4, U4.3 (-)
GND: C10.2, J1.3, P2.1, P4.5, P4.6, P5.4, P6.1, P9.1, P9.2, R13.2, R15.2, R16.1, U1.9 (GND), U1.15 (GND), U2.1 (In-), U2.3 (Out-), U3.2 (V-), U4.2 (V-)
Hsync: P9.23, R12.1, R16.2
LASER_DATA: J1.2, P9.17
MIRROR_CLK: P5.1, P9.18
unnamed: C1.2, P2.2, R14.2, U3.3 (-)
unnamed: P3.2, U1.4 (MS3)
unnamed: P3.4, U1.3 (MS2)
unnamed: P3.6, U1.2 (MS1)
unnamed: P4.7, U1.14 (2B)
unnamed: P4.8, U1.11 (1B)
unnamed: P4.9, U1.13 (2A)
unnamed: P4.10, U1.12 (1A)
unnamed: R10.2, R11.2, R15.1, U4.1 (+)
unnamed: R9.2, R13.1, U3.1 (+)
SLED_DIR: P9.14, U1.8 (DIR)
SLED_STEP: P9.15, U1.7 (STEP)
~MOTORS_EN: P5.3, P9.16, R1.2, U1.1 (~ENABLE)
~StopBack: P4.4, P9.12, R4.1
~StopFront: P4.3, P9.13, R2.1
~UI-Button: P4.2, P9.11, R3.1

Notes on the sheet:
Schmitt Trigger
Photo Diode Amp

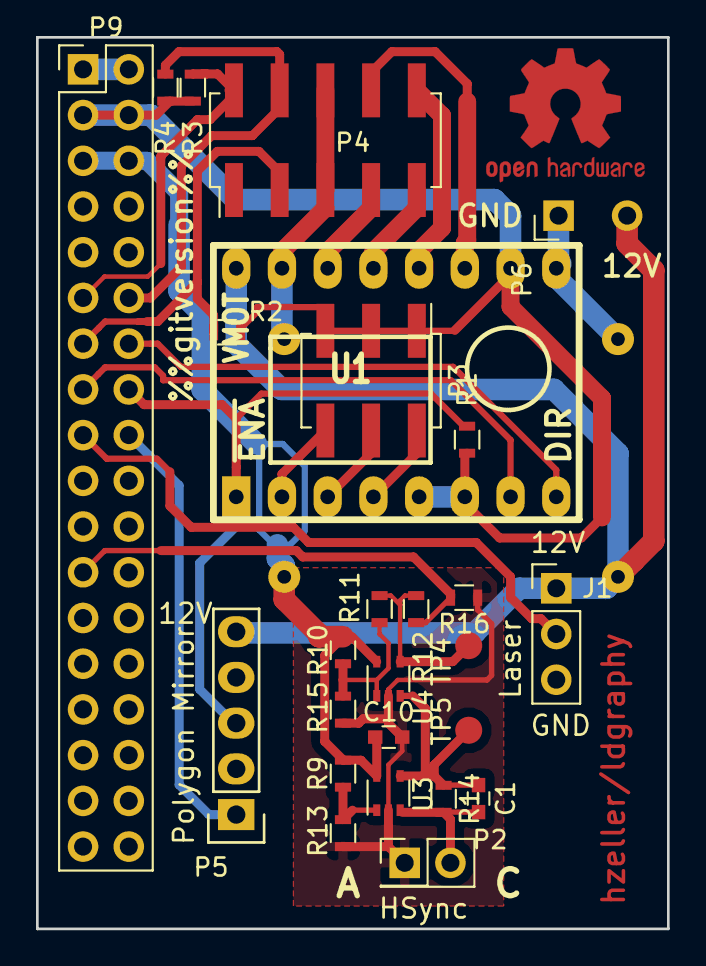
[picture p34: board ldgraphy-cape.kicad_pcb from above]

Board: 2 copper layers, 35.1 x 49.5 mm, 27 parts (1 on the bottom side), 25 nets.

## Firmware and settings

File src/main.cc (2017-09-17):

/* -*- mode: c++; c-basic-offset: 4; indent-tabs-mode: nil; -*-
 * (c) 2017 Henner Zeller <h.zeller@acm.org>
 *
 * This file is part of LDGraphy http://github.com/hzeller/ldgraphy
 *
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
 * You should have received a copy of the GNU General Public License
 * along with LDGraphy.  If not, see <http://www.gnu.org/licenses/>.
 */

#include <assert.h>
#include <math.h>
#include <signal.h>
#include <stdint.h>
#include <stdio.h>
#include <stdlib.h>
#include <string.h>
#include <strings.h>
#include <time.h>
#include <unistd.h>

#include <memory>
#include <vector>

#include "containers.h"
#include "image-processing.h"
#include "laser-scribe-constants.h"
#include "ldgraphy-scanner.h"
#include "scanline-sender.h"
#include "sled-control.h"

constexpr float kThinningChartResolution = 0.005; // mm per pixel
constexpr float kInitialSledOffsetMM = 3; // sled skip initial markings.

// Interrupt handling. Provide a is_interrupted() function that reports
// if Ctrl-C has been pressed. Requires ArmInterruptHandler() called before use.
bool s_handler_installed = false;
volatile bool s_interrupt_received = false;
static void InterruptHandler(int) {
  s_interrupt_received = true;
}
static void ArmInterruptHandler() {
    if (!s_handler_installed) {
        signal(SIGTERM, InterruptHandler);
        signal(SIGINT, InterruptHandler);
        s_handler_installed = true;
    }
    s_interrupt_received = false;
}
static bool is_interrupted() { return s_interrupt_received; }
static void DisarmInterruptHandler() {
    signal(SIGTERM, SIG_DFL);
    signal(SIGINT, SIG_DFL);
}

static int usage(const char *progname, const char *errmsg = NULL) {
    if (errmsg) {
        fprintf(stderr, "\n%s\n\n", errmsg);
    }
    fprintf(stderr, "Usage:\n%s [options] <png-image-file>\n", progname);
    fprintf(stderr, "Options:\n"
            "\t-d <val>   : Override DPI of input image. Default -1\n"
            "\t-i         : Inverse image: black becomes laser on\n"
            "\t-x<val>    : Exposure factor. Default 1.\n"
            "\t-o<val>    : Offset in sled direction in mm\n"
            "\t-R         : Quarter image turn left; "
            "can be given multiple times.\n"
            "\t-h         : This help\n"
            "Mostly for testing or calibration:\n"
            "\t-S         : Skip sled loading; assume board already loaded.\n"
            "\t-E         : Skip eject at end.\n"
            "\t-F         : Run a focus round until Ctrl-C\n"
            "\t-M         : Testing: Inhibit sled move.\n"
            "\t-n         : Dryrun. Do not do any scanning; laser off.\n"
            "\t-j<exp>    : Mirror jitter test with given exposure repeat\n"
            "\t-D<line-width:start,step> : Laser Dot Diameter test chart.\n"
            "\t\tCreates a test-strip 10cm x 2cm with 10 samples with 'line-width' trace/clearance.\n"
            "\t\tApply thinning to line beginning with 'start', increase for each of the 10 samples by 'step'. e.g. -D0.15:0.04,0.01\n");
    return errmsg ? 1 : 0;
}

// Given an image filename, create a LDGraphyScanner that can be used to expose
// that image.
bool LoadImage(LDGraphyScanner *scanner,
               const char *filename, float override_dpi,
               bool invert, int quarter_turns) {
    if (!filename) return false;
    double input_dpi = -1;
    std::unique_ptr<BitmapImage> img(LoadPNGImage(filename, invert, &input_dpi));
    if (img == nullptr) return false;

    if (override_dpi > 0 || input_dpi < 100 || input_dpi > 20000)
        input_dpi = override_dpi;

    if (input_dpi < 100 || input_dpi > 20000) {
        fprintf(stderr, "Couldn't extract usable DPI from image. "
                "Please provide -d <dpi>\n");
        return false;
    }

    while (quarter_turns--)
        img.reset(CreateRotatedImage(*img));

    return scanner->SetImage(img.release(), 25.4 / input_dpi);
}

// Output a line with dots in regular distance for testing the set-up.
void RunFocusLine(LDGraphyScanner *scanner) {
    // Essentially, we want a one-line image of known resolution with regular
    // pixels set.
    constexpr int bed_width = 100;   // 100 mm bed
    constexpr int res = 10;          // 1/10 mm resolution
    constexpr int mark_interval = 5; // every 5 mm
    BitmapImage *img = new BitmapImage(1, bed_width * res);
    for (int mm = 0; mm < bed_width; mm += mark_interval) {
        img->Set(0, mm * res, true);
    }
    scanner->SetImage(img, 0.01);
    ArmInterruptHandler();
    while (!is_interrupted()) {
        if (!scanner->ScanExpose(false,
                                 [](int, int) { return !is_interrupted(); })) {
            break;
        }
    }
    fprintf(stderr, "Focus run done.\n");
}

void UIMessage(const char *msg) {
    fprintf(stdout, "**********> %s\n", msg);
}

int main(int argc, char *argv[]) {
    double commandline_dpi = -1;
    bool dryrun = false;
    bool invert = false;
    bool do_focus = false;
    bool do_move = true;
    bool do_sled_loading_ui = true;
    bool do_sled_eject = true;
    std::unique_ptr<BitmapImage> dot_size_chart;

    int quarter_turns = 0;
    int mirror_adjust_exposure = 0;
    float offset_x = 0;
    float exposure_factor = 1.0f;

    int opt;
    while ((opt = getopt(argc, argv, "MFhnid:x:j:o:SERD:")) != -1) {
        switch (opt) {
        case 'h': return usage(argv[0]);
        case 'd':
            commandline_dpi = atof(optarg);
            break;
        case 'n':
            dryrun = true;
            break;
        case 'i':
            invert = true;
            break;
        case 'F':
            do_focus = true;
            break;
        case 'M':
            do_move = false;
            break;
        case 'x':
            exposure_factor = atof(optarg);
            break;
        case 'j':
            mirror_adjust_exposure = atoi(optarg);
            break;
        case 'o':
            offset_x = atof(optarg);   // TODO: also y. as x,y coordinate.
            break;
        case 'S':
            do_sled_loading_ui = false;
            break;
        case 'E':
            do_sled_eject = false;
            break;
        case 'R':
            quarter_turns++;
            break;
        case 'D': {
            float line_w, start, step;
            if (sscanf(optarg, "%f:%f,%f", &line_w, &start, &step) == 3) {
                dot_size_chart.reset(
                    CreateThinningTestChart(kThinningChartResolution,
                                            line_w, 10, start, step));
            } else {
                return usage(argv[0], "Invalid Laser dot diameter chart params");
            }
            break;
        }

        }
    }

    const char *filename = nullptr;

    if (argc > optind+1)
        return usage(argv[0], "Exactly one image file expected");
    if (argc == optind + 1) {
        filename = argv[optind];
    }

    if (exposure_factor < 1.0f) {
        return usage(argv[0], "Exposure factor needs to be at least 1.");
    }

    if (filename && dot_size_chart) {
        return usage(argv[0], "You can either expose an image or create a "
                     "dot size chart, but not both.");
    }

    if (!filename && !do_focus && !mirror_adjust_exposure && !dot_size_chart)
        return usage(argv[0]);   // Nothing to do.

    fprintf(stdout, "LDGraphy Copyright (C) 2017 Henner Zeller | http://ldgraphy.org/\n"
            "This program comes with ABSOLUTELY NO WARRANTY.\n"
            "This is free software and hardware, and you are welcome to "
            "redistribute\nand modify it if the conditions of the GPL version 3 "
            "are met.\n"
            "See https://www.gnu.org/licenses/gpl.txt for details.\n\n");

    bool do_image = false;
    LDGraphyScanner *ldgraphy = new LDGraphyScanner(exposure_factor);
    if (dot_size_chart) {
        do_image = true;
        ldgraphy->SetLaserDotSize(0, 0);  // Chart already thinned image.
        ldgraphy->SetImage(dot_size_chart.release(), kThinningChartResolution);
    } else {
        do_image = LoadImage(ldgraphy, filename,
                             commandline_dpi, invert, quarter_turns  % 4);
        if (filename && !do_image) return 1;  // Got file, but failed loading.
    }

    if (do_image) {
        const int eta = ldgraphy->estimated_time_seconds();
        fprintf(stderr, "Estimated exposure time: %d:%02d min "
                "(%.1fmm/min, "
                // We don't actually know the optical power output of the
                // laser diode, so let's just give it as comparative figure.
                //"%.0fmJ/cm²)\n",
                "normalized %.0f energy units/area)\n",
                eta / 60, eta % 60, ldgraphy->exposure_speed_mm_per_sec() * 60,
                ldgraphy->exposure_joule_per_cm2() * 1000);
    }

    SledControl sled(4000, do_move && !dryrun);

    // Super-crude UI
    if (do_sled_loading_ui) {
        UIMessage("Hold on .. sled to take your board is on the way...");
        sled.Move(180);  // Move all the way out for person to place device.
        UIMessage("Here we are. Please place board in (0,0) corner. Press <RETURN>.");
        while (fgetc(stdin) != '\n')
            ;
        UIMessage("Thanks. Getting ready to scan.");
    }

    sled.Move(-180);   // Back to base.

    float forward_move = kInitialSledOffsetMM;  // Forward until we reach begin.
    if (mirror_adjust_exposure) forward_move += 5;
    forward_move += offset_x;
    sled.Move(forward_move);

    ArmInterruptHandler();  // While PRU running, we want controlled exit.
    ScanLineSender *line_sender = dryrun
        ? new DummyScanLineSender()
        : PRUScanLineSender::Create();
    if (!line_sender) {
        fprintf(stderr, "Cannot initialize hardware.\n");
        return 1;
    }

    ldgraphy->SetScanLineSender(line_sender);

    if (mirror_adjust_exposure) {
        ldgraphy->ExposeJitterTest(6, mirror_adjust_exposure);
    }

    if (do_focus) {
        fprintf(stderr, "== FOCUS run. Exit with Ctrl-C. ==\n");
        RunFocusLine(ldgraphy);
    }

    if (do_image) {
        fprintf(stderr, "== Exposure. Emergency stop with Ctrl-C. ==\n");
        int prev_percent = -1, prev_remain_time = -1;
        const float total_sec = ldgraphy->estimated_time_seconds();
        ldgraphy->ScanExpose(
            do_move,
            [&prev_percent, &prev_remain_time, total_sec](int done, int total) {
                // Simple commandline progress indicator.
                const int percent = roundf(100.0 * done / total);
                const int remain_time = roundf(total_sec -
                                               (total_sec * done / total));
                // Only update if any number would change.
                if (percent != prev_percent || remain_time != prev_remain_time) {
                    fprintf(stderr, "\b\b\b\b\b\b\b\b\b\b\b\b\b\b\b\b\b\b\b\b"
                            "%3d%%; %d:%02d left ",
                            percent, remain_time / 60, remain_time % 60);
                    fflush(stderr);
                    prev_percent = percent;
                    prev_remain_time = remain_time;
                }
                return !is_interrupted();
            });
        if (is_interrupted())
            fprintf(stderr, "Interrupted. Exposure might be incomplete.\n");
    }

    delete ldgraphy;  // First make PRU stop using our pins.

    DisarmInterruptHandler();   // Everything that comes now: fine to interrupt

    if (do_sled_eject) {
        UIMessage("Done Scanning - sending the sled with the board towards you.");
        sled.Move(180);  // Move out for user to grab.

        UIMessage("Here we are. Please take the board and press <RETURN>");
        // TODO: here, when the user takes too long, just pull in board again
        // to have it more protected against light.
        while (fgetc(stdin) != '\n')
            ;
        UIMessage("Thanks. Going back.");
        sled.Move(-85);
    }

    return 0;
}

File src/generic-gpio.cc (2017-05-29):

/* -*- mode: c; c-basic-offset: 2; indent-tabs-mode: nil; -*-
 * (c) 2013, 2014 Henner Zeller <h.zeller@acm.org>
 *
 * This file is part of BeagleG. http://github.com/hzeller/beagleg
 *
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
 * You should have received a copy of the GNU General Public License
 * along with BeagleG.  If not, see <http://www.gnu.org/licenses/>.
 */

#include <stdint.h>
#include <stdio.h>
#include <fcntl.h>
#include <sys/mman.h>
#include <unistd.h>

#include "generic-gpio.h"

// GPIO Registers
#define GPIO_OE           0x134
#define GPIO_DATAIN       0x138
#define GPIO_DATAOUT      0x13c
#define GPIO_CLEARDATAOUT 0x190
#define GPIO_SETDATAOUT   0x194

// Memory space mapped to the Clock Module registers
#define CM_BASE                 0x44e00000
#define CM_SIZE                 0x4000

// Clock Module Peripheral and Wakeup registers
#define CM_WKUP_GPIO0_CLKCTRL   (0x400 + 0x008)
#define CM_PER_GPIO1_CLKCTRL    (0x000 + 0x0ac)
#define CM_PER_GPIO2_CLKCTRL    (0x000 + 0x0b0)
#define CM_PER_GPIO3_CLKCTRL    (0x000 + 0x0b4)

#define IDLEST_MASK             (0x03 << 16)
#define MODULEMODE_ENABLE       (0x02 << 0)

#define GPIO_MMAP_SIZE 0x2000

// GPIO registers.
static volatile uint32_t *gpio_0 = NULL;
static volatile uint32_t *gpio_1 = NULL;
static volatile uint32_t *gpio_2 = NULL;
static volatile uint32_t *gpio_3 = NULL;

static volatile uint32_t *get_gpio_base(uint32_t gpio_def) {
  switch (gpio_def & 0xfffff000) {
  case GPIO_0_BASE: return gpio_0;
  case GPIO_1_BASE: return gpio_1;
  case GPIO_2_BASE: return gpio_2;
  case GPIO_3_BASE: return gpio_3;
  default: return NULL;
  }
}

int get_gpio(uint32_t gpio_def) {
  volatile uint32_t *gpio_port = get_gpio_base(gpio_def);
  uint32_t bitmask = 1 << (gpio_def & 0x1f);
  uint32_t status;

  if (gpio_port) {
    status = gpio_port[GPIO_DATAIN/4];
    return (status & bitmask) ? 1 : 0;
  }
  return -1;
}

void set_gpio(uint32_t gpio_def) {
  volatile uint32_t *gpio_port = get_gpio_base(gpio_def);
  uint32_t bitmask = 1 << (gpio_def & 0x1f);
  if (gpio_port)
    gpio_port[GPIO_SETDATAOUT/4] = bitmask;
}

void clr_gpio(uint32_t gpio_def) {
  volatile uint32_t *gpio_port = get_gpio_base(gpio_def);
  uint32_t bitmask = 1 << (gpio_def & 0x1f);
  if (gpio_port)
    gpio_port[GPIO_CLEARDATAOUT/4] = bitmask;
}

static void set_gpio_mask(uint32_t *mask, uint32_t gpio_def) {
  const uint32_t bitmask = 1 << (gpio_def & 0x1f);
  switch (gpio_def & 0xfffff000) {
  case GPIO_0_BASE: mask[0] |= bitmask; break;
  case GPIO_1_BASE: mask[1] |= bitmask; break;
  case GPIO_2_BASE: mask[2] |= bitmask; break;
  case GPIO_3_BASE: mask[3] |= bitmask; break;
  }
}

// TODO: have at central place, right now it is tow places
#define SLED_MOTOR_STEP (GPIO_1_BASE | 16)
#define SLED_MOTOR_DIR (GPIO_1_BASE | 18)
#define SLED_MOTOR_ENABLE (GPIO_1_BASE | 19)

#define SLED_ENDSWITCH_FRONT (GPIO_0_BASE | 31)
#define SLED_ENDSWITCH_BACK (GPIO_1_BASE | 28)

static void cfg_gpio_io() {
  uint32_t output_mask[4] = { 0, 0, 0, 0 };

  // All the gpio's we need from userspace (PRU will do its own)
  set_gpio_mask(output_mask, SLED_MOTOR_ENABLE);
  set_gpio_mask(output_mask, SLED_MOTOR_DIR);
  set_gpio_mask(output_mask, SLED_MOTOR_STEP);

  uint32_t input_mask[4] = { 0, 0, 0, 0 };
  set_gpio_mask(input_mask, SLED_ENDSWITCH_FRONT);
  set_gpio_mask(input_mask, SLED_ENDSWITCH_BACK);

  // Preserve GPIO output settings that might already be set by other tasks,
  // so we only selectively set the bits we are interested in.

  // Set the output enable register for each GPIO bank.
  // Output direction is signified with a zero.
  gpio_0[GPIO_OE/4] &= ~output_mask[0];
  gpio_1[GPIO_OE/4] &= ~output_mask[1];
  gpio_2[GPIO_OE/4] &= ~output_mask[2];
  gpio_3[GPIO_OE/4] &= ~output_mask[3];

  // All the inputs we need. Inputs are signified with a one.
  gpio_0[GPIO_OE/4] |= input_mask[0];
  gpio_1[GPIO_OE/4] |= input_mask[1];
  gpio_2[GPIO_OE/4] |= input_mask[2];
  gpio_3[GPIO_OE/4] |= input_mask[3];
}

static volatile uint32_t *map_port(int fd, size_t length, off_t offset) {
  return (volatile uint32_t*) mmap(0, length, PROT_READ | PROT_WRITE, MAP_SHARED, fd, offset);
}

static void ena_gpio_clk(volatile uint32_t *cm, uint32_t reg, int) {
  uint32_t val;

  val = cm[reg/4];
  if (val & IDLEST_MASK) {
    val |= MODULEMODE_ENABLE;
    cm[reg/4] = val;
    do {
      val = cm[reg/4];
    } while (val & IDLEST_MASK);
  }
}

static int enable_gpio_clocks(int fd) {
  volatile uint32_t *cm;

  cm = map_port(fd, CM_SIZE, CM_BASE);
  if (cm == MAP_FAILED) { perror("mmap() CM"); return 0; }

  ena_gpio_clk(cm, CM_WKUP_GPIO0_CLKCTRL, 0);
  ena_gpio_clk(cm, CM_PER_GPIO1_CLKCTRL, 1);
  ena_gpio_clk(cm, CM_PER_GPIO2_CLKCTRL, 2);
  ena_gpio_clk(cm, CM_PER_GPIO3_CLKCTRL, 3);

  munmap((void*)cm, CM_SIZE);
  return 1;
}
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

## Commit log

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2017-01-01 o Add motor mount.
    [motor-mount.dxf]
2017-01-01 o Motor mount with axis hole.
    [motor-mount.dxf]
2017-01-01 o Add side mount.
    [side-mount.dxf]
2017-01-01 o side-mount without 'nose'
    [side-mount2.dxf]
2017-01-01 o add polygon mirror mount.
    [rot-mirror-mount.dxf]
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2017-01-03 o Prepare DTS for more output bits (for the sled stepper motor) o Make PRU code more readable by assigning some variables to fixed registers and name them using the .struct feature.
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2017-01-05 o Fix timing of mirror: the mirror only needs a pulse every other mirror face. o While at it, decouple the mirror cycle from the data cycle so that it has its own count and phase offset. o tighten ti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
    [laser-scribe-constants.h, main.cc]
2017-01-06 o More queing to avoid unnecessary buffer underruns.
    [laser-scribe-constants.h]
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2017-01-07 o Updates for cuts.
    [sled.dxf, spacers.dxf]
2017-01-09 o add acme screw holder (Thanks to Miloh).
    [acme-square-nut-mold.scad]
2017-01-09 o Starting a cape for the Beaglebone.
    [ldgraphy-cape.kicad_pcb, ldgraphy-cape.sch]
2017-01-22 o Remove first generation laser cut parts.
    [acme-square-nut-mold.scad, laser-rot-mount.dxf, motor-mount.dxf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]
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2017-02-05 o Move cape in separate directory.
    [ldgraphy-cape.kicad_pcb, ldgraphy-cape.sch]
2017-02-05 o add hsync sensor.
    [hsync-sense.kicad_pcb, hsync-sense.sch]
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2017-02-11 o Update resistor values.
    [hsync-sense.kicad_pcb, hsync-sense.sch]
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2017-02-14 o Refine test pattern: new goal of 0.1mm to have a margin for typical needed resolution. o Correct for some over-thickness of lines that ghostscript creates when rendering bitmaps.
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2017-02-25 o Move image processing related stuff to image-proscessing.{h,cc} o Move scanning logic into ldgraphy-scanner.{h,cc} o reformultate focus line in terms of an image. o Add some callbacks for interrupt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
    [main.cc]
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2017-03-05 o Fix drive-train missing fingers.
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2017-03-15 o avoid issues with 'maybe' fingers due to rounding errors.
2017-03-17 o Add laser driver (old version)
    [laser-drive.kicad_pcb, laser-drive.sch]
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2017-03-26 o laser driver: change to use OpAmp.
    [laser-drive.sch]
2017-03-28 o Update cape: include hsync circuit o Laser driver: new board that uses the new OpAmp circuit (not tested yet)
    [laser-drive.kicad_pcb, laser-drive.sch, ldgraphy-cape.kicad_pcb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]
2017-03-28 o Add pictures for laser driver.
    [laser-drive.sch]
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2017-03-28 o Add reference SC70 3D package.
    [laser-drive.kicad_pcb]
2017-03-28 o Add more copper to cool main transistor.
    [laser-drive.kicad_pcb]
2017-03-31 o Fix issues with overlapping copper planes.
    [laser-drive.kicad_pcb]
2017-03-31 o Add a direct GND trace from connector to capacitors.
    [laser-drive.kicad_pcb]
2017-04-01 o Add more clearance around GND between pins of SC70
    [laser-drive.kicad_pcb]
2017-04-01 o Update PCB renderings.
    [laser-drive.kicad_pcb]
2017-04-02 o Change footprint trimmer to actual size.
    [laser-drive.kicad_pcb, laser-drive.sch]
2017-04-02 o Update footprint resistor.
    [laser-drive.kicad_pcb, laser-drive.sch]
2017-04-06 o Sketch out cape. NB: different GPIO assignment than current software expects.
    [ldgraphy-cape.kicad_pcb, ldgraphy-cape.sch]
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2017-04-21 Fix rotation of sled outline (springs were on the wrong side).
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2017-05-29 Provide loading feature making it simple to enter and remove board.
    o Simple user-space stepper control for the sled. This is only really
    useful for testing, as the timing is of course jittery in non-realtime.
    [generic-gpio.cc, main.cc, sled-control.cc]
2017-05-29 Add mirror tilt jitter test exposure; provide offset option.
    o The mirrors in some polygon mirrors have slight tilt errors
    resulting in jitter in the sled direction. Add an option that
    creates an exposure line in which each mirror face is responsible
    for one part of the line; the resulting 'steps' between lines is
    the error (preparation for later correcting for that).
    o Add an option to start exposure with an offset in sled direction.
    Allows for multiple exposure tests.
    [main.cc]
2017-05-30 Provide an option to skip initial load phase.
    [main.cc]
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2017-05-31 Updating comments; tweaking some values
    o Update comments in PRU code for better documentation.
    o Tweak timing values and measure current line rate.
    o Better handling of errors in scanning to stop focus line when
    there are issues.
    [laser-scribe-constants.h, main.cc]
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2017-06-04 Non-tented via for laser driver for single-sided etching.
    [laser-drive.kicad_pcb]
2017-06-04 Allow to set ScanBackend later for LDGraphyScanner.
    o In order to show the image loading information on start-up,
    allow that LDGraphyScanner can be consructed without a backend
    available at fist, so that we can call SetImage() on it early.
    o The actual ScanLineSender setting happens after initial validation
    is done to avoid messing with the hardware before needed.
    [main.cc]
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2017-06-06 Removal: Don't need old hsync-sense anymore. This is now part of the cape.
    [hsync-sense.kicad_pcb, hsync-sense.sch]
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2017-06-10 Universally use mm/pixel as resolution. Fix SetLaserDotSize() bug.
    o SetLaserDotSize() was not assigning scan_dot_size.
    [main.cc]
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2017-06-11 ConvertBlackWhite: fix bug; ThinImageStructures: don't overwrite currently read image.
    o ConvertBlackWhite: initialization error of the bitmask variable.
    o ThinImageStructure: make work as before - don't change value of pixel
    while we read from image (worked before because we used multi-levels)
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2017-06-15 Use as low as possible laser modulation while mirror is still smoothly turning.
    o Looks like some states in the state machine take longer than planned,
    partially due to the crazy overhead trying to get a CPU cycle out of
    the PRU. Choose large enough number that everything fits in alotted
    slot (TODO: hunt down cpu-waster. The bit-loop is known to be too
    wasteful).
    o Lower laser frequency means possibly higher definition depening on how
    fast the laser switches the photon output.
    o There is a lower limit: the mirror starts to get jerky when driven
    too slow.
    [laser-scribe-constants.h]
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2017-06-18 Test image: resolution of scan line.
    o Mirror jitter matters and can make a line get worse over its
    progress. Also focus of course. This test image helps to
    test that.
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2017-06-20 Provide some more useful informatione when image does not fit.
    o If non-fit: Show if it would fit if we rotated the image.
    o More info about progress of image processing (thinning takes some
    time, so expose that optimization opportunity).
    [main.cc]
2017-06-21 Provide status byte PRU->Host; some optimizations.
    o Have a byte that we can send back from PRU to the Host, such as
    error states. This way we can distinguish various error states.
    o Whenever we run out of time for a state, fail immediately with
    an error state so that this is noticeable and can be optimized.
    o Optimize a little. Read laser via r31 instead of GPIO input which
    seems to be pretty slow.
    o Reduce TICK_DELAY from 110 -> 70 again as a too slow polygon mirror
    seems to start showing cogging and is more inaccurate towards the
    end of the throw.
    [laser-scribe-constants.h]
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2017-09-10 Add oscillation suppresion cap for laser driver.
    [laser-drive.kicad_pcb, laser-drive.sch]
2017-09-10 Add photo diode compensating cap in feedback loop.
    [ldgraphy-cape.kicad_pcb, ldgraphy-cape.sch]
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2017-09-30 Adjust header distance to accomodate space to use JST XH headers.
    [pocket-cape.kicad_pcb, pocket-cape.sch]
2017-09-30 Move component labels for better readability.
    Also add signal labels on the PocketBeagle header for easier testpoint
    finding.
    [pocket-cape.kicad_pcb, pocket-cape.sch]
2017-09-30 Fix wrong connection to stepper connector.
    o common is not the center tap, but Pin5
    o Also some more labelling (e.g. adding RX/TX)
    [pocket-cape.kicad_pcb, pocket-cape.sch]
2017-09-30 Use three-way connector for Laser (GND - signal - 12V)
    [pocket-cape.kicad_pcb, pocket-cape.sch]
2017-10-01 Simplyfy photo diode sync input.
    o The 74LVC14 inputs are sufficiently high impedance that we
    can directly connect the photo input.
    o Also: switch to JST PH 2mm connectors for laser output.
    [pocket-cape.kicad_pcb, pocket-cape.sch]
2017-10-05 Intermediate state: initial display and USB connector.
    o Add flat flex connector to drive a simple SPI-based display.
    o Try to cram a vertial USB connector onto the board to be able
    to have a wifi dongle.
    [pocket-cape.kicad_pcb, pocket-cape.sch]
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2017-10-05 Add a capacitor in the stepper driver vicinity.
    [pocket-cape.kicad_pcb, pocket-cape.sch]
2017-10-05 Improve silkscreen.
    o Label signals directly on header for easier measurements.
    o Arrange partially obstructed component labels.
    [pocket-cape.kicad_pcb]
2017-10-05 Connect to more local GND on Hsync stabilizing cap.
    [pocket-cape.kicad_pcb]
2017-10-08 Little tweaks (silk-screen; adding 100nF on 3.3V rail)
    [pocket-cape.kicad_pcb, pocket-cape.sch]
2017-10-08 Get 0.2mm clearance throughout.
    [pocket-cape.kicad_pcb]
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2017-10-08 Move P1 reference where it is on the PocketBeagle board for easier matching.
    [pocket-cape.kicad_pcb]
2017-10-08 Remove unneccessary inner layers.
    o There were inner layers left-over from basing this on the PocketBeagle.
    Just keep Top/Bottom.
    o Remove leftover text from inner layers.
    [pocket-cape.kicad_pcb]
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2017-10-29 Update values in Schematic; directly connect USB 5V with DC/DC 5V.
    [pocket-cape.kicad_pcb, pocket-cape.sch]
2017-10-29 Connect USB output to SYS 5V
    o SYS 5V has a cleaner switch-on transition than the raw DC/DC out.
    [pocket-cape.kicad_pcb, pocket-cape.sch]
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2017-10-29 Label motor phases on GPIO header for easier measurements.
    [pocket-cape.kicad_pcb]
2017-10-29 More cooling for ULN2003
    o Connect unused pins to a GND copper plane for slightly better
    heat distribution (in any case, we are well within ratings
    of the chip; the sum of all currents is never more than 500mA).
    [pocket-cape.kicad_pcb, pocket-cape.sch]
2017-10-30 More via stitching between GND planes.
    Mostly to heatsink ULN2003, but also in other places to reduce
    impedance.
    [pocket-cape.kicad_pcb]
2017-11-01 Put a ground-plane near power connector under switcher.
    [pocket-cape.kicad_pcb]
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2023-07-23 Update fab script to work with current KiCAD
    [laser-drive.kicad_pcb]
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2023-07-23 Update transistor that is out of production.
    MTM232270 -> DMN2058UW
    [laser-drive.kicad_sch]
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

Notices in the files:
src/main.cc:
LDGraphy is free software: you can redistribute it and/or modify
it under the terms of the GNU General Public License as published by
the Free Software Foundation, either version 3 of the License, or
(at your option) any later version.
